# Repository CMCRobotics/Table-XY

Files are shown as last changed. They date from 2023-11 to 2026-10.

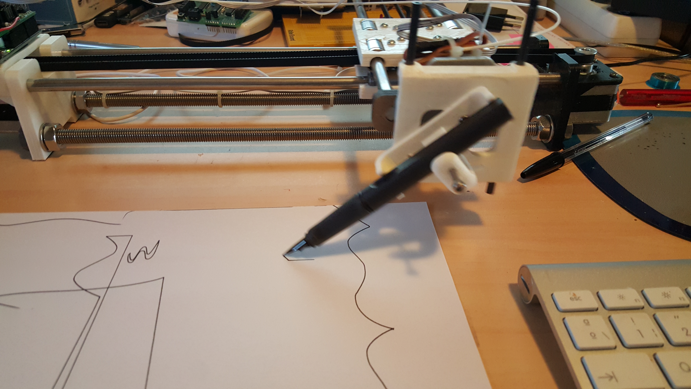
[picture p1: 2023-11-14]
mechanic/docs/Images General/2016-04-07_18.31.24.jpg

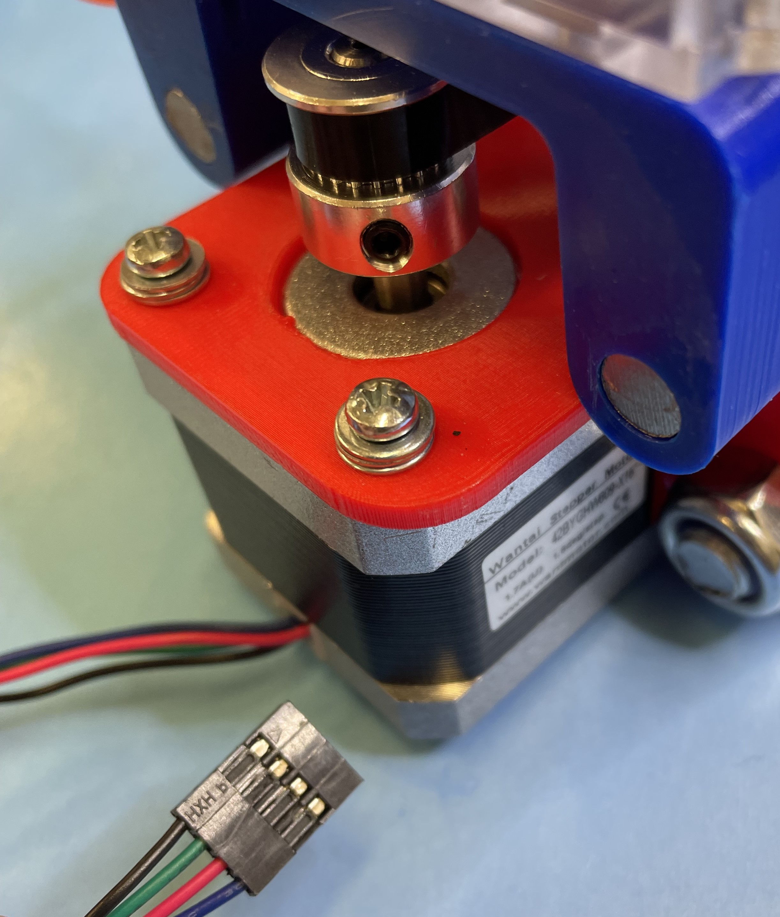
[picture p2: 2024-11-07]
assembly/Photos/IMG_9785.JPG

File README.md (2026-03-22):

# Table-XY
Development of a Table XY based on 4xiDraw

Directories:
- docs: 
- 	General documents

- components: 
- 	Components to be bought, related actions

- hardware: 
- 	documents related to Electronic hardware

- mechanic: 
-	Mechanic elements
-     mechanic / docs: documents related to mechanic elements
-     mechanic / Files: documents related to mechanical elements
-     mechanic / Printer3D-Prusa: documents related to Prusa Printer-3D

- photos: 
-	Photos of the assembly steps

- software: 
-	programs and related elements
-     software / docs: documents
-     software / Arduino: Arduino related programs

- wiki: 
-	elements for wiki page
-     wiki / images: Images
-     wiki / docs: Documents.

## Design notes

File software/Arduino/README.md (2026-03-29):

# Table-XY
Development of Arduino programs

Directories:
- UNO: 
-	programs related to Arduino UNO component
- 		UNO / grbl-servo-master: Original grbl-servo-master with M3/M5 action 
- 		UNO / TableXY_grbl: Modified grbl-servo-master transforming Zaxis movements into M3/M5 up/down pencil actions. IN DEVELOPEMENT
-							Versions.txt: details the modifications

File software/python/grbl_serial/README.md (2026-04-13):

# Serial GRBL

Python program for exchanging CGode files with a GRBL based device 

Based on simple_stream.py from https://github.com/gnea/grbl v1.1h

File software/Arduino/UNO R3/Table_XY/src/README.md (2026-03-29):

-------------------------------------------------------------------

Program modified by Jose Luis Gomez Costa, for converting Zaxis commands into Pencil up/down commands

	When Z command is detected in a Command line:
		- Mxx command is executed, depending on the value of Z movement:
			Z positive is Pencil up
			Z negative is Pencil down
			Only the sign is checked.
		- then the original command line is executed unmodified.
		
	This will imply always processing the Z axis, but as there is no hardware it will not interfere with the actual behaviour with a Pencil.

-------------------------------------------------------------------
# grbl-servo Original
grbl 0.9i with Servo motor support

GRBL 0.9i with servo motor support.
Use the PIN D11 to drive the servo. 
Use the commands M03 Sxxx (xxx between 0 and 255) to rotate the servo between 0-180.
The command M05 turn the servo to zero degrees.

you can change the pulse duration in the file spindle_control.c:

define RC_SERVO_SHORT     15       // Timer ticks for 0.6ms pulse duration  (9 for 0.6ms)

define RC_SERVO_LONG      32       // Timer ticks for 2.5 ms pulse duration  (39 for 2.5ms)     

define RC_SERVO_INVERT     1     // Uncomment to invert servo direction

If you want to have the servo working from 0 --> 180 degrees change RC_SERVO_SHORT and put 9, RC_SERVO_LONG and put 39
If you want invert the servo direction uncomment the line above.

I tested the code very well with 328p (Arduino Uno, Duemilanove etv), not with 2560 (Arduino Mega), but I think it would work well also with the Mega.

-------------------------------------------------------------------

The link for GRBL vanilla is: http://github.com/grbl/grbl

Grbl is a no-compromise, high performance, low cost alternative to parallel-port-based motion control for CNC milling. It will run on a vanilla Arduino (Duemillanove/Uno) as long as it sports an Atmega 328.

The controller is written in highly optimized C utilizing every clever feature of the AVR-chips to achieve precise timing and asynchronous operation. It is able to maintain up to 30kHz of stable, jitter free control pulses.

It accepts standards-compliant g-code and has been tested with the output of several CAM tools with no problems. Arcs, circles and helical motion are fully supported, as well as, all other primary g-code commands. Macro functions, variables, and most canned cycles are not supported, but we think GUIs can do a much better job at translating them into straight g-code anyhow.

Grbl includes full acceleration management with look ahead. That means the controller will look up to 18 motions into the future and plan its velocities ahead to deliver smooth acceleration and jerk-free cornering.

Licensing: Grbl is free software, released under the GPLv3 license.

For more information and help, check out our Wiki pages! If you find that the information is out-dated, please to help us keep it updated by editing it or notifying our community! Thanks!

Lead Developer [2011 - Current]: Sungeun(Sonny) K. Jeon, Ph.D. (USA) aka @chamnit

Lead Developer [2009 - 2011]: Simen Svale Skogsrud (Norway). aka The Originator/Creator/Pioneer/Father of Grbl.

The link for GRBL vanilla is: http://github.com/grbl/grbl

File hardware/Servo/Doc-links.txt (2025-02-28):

https://protosupplies.com/product/servo-motor-micro-sg92r/
https://forum.phpoc.com/articles/tutorials/347-servo-motor-how-to-control-servo-motor

https://docs.arduino.cc/learn/electronics/servo-motors/
Servo Hardware: https://en.wikipedia.org/wiki/Servo_(radio_control)

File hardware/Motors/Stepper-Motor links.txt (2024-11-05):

Half/Full step:
https://sea.omega.com/th/prodinfo/stepper_motors.html
https://www.automate.org/motion-control/case-studies/what-is-the-difference-between-full-stepping-the-half-stepping-and-the-micro-drive
Arduno: half/Full step: https://www.youtube.com/watch?v=cYAPK7xoISE

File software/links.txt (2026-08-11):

---------------------------------------------------------------------------
Description files: https://www.instructables.com/4xiDraw/General

---------------------------------------------------------------------------
Universal GCode sender: 
		https://universalgcodesender.com/
		https://github.com/winder/Universal-G-Code-Sender?tab=readme-ov-file
		
		UGS Platform (Rich): Run directly the exe in d:\Hobby\GRBL\ugsplatform-win\bin\
		UGS Clasic: Simple for sending direct commands to the Controller. Requires JAVA 61

---------------------------------------------------------------------------

Display/Simulate GCode work https://camotics.org/

---------------------------------------------------------------------------
GRBL: https://github.com/grbl/grbl/tree/master/grbl
      https://github.com/gnea/grbl
	  
GRBL updates: https://github.com/gnea
GRBL 1.1 https://github.com/gnea/grbl

GRBL 0.9 https://github.com/grbl/grbl/wiki/Configuring-Grbl-v0.9

GRBL 0.9i with Servo motor support: https://github.com/misan/grbl-servo

Pilot CNC via GCode with Arduino: https://letmeknow.fr/fr/blog/110-tuto-piloter-une-cnc-avec-arduino-et-grbl

Arduino Forum for GRBL: https://forum.arduino.cc/t/arduino-uno-r4-minima-grbl-upload-error/1385989

GRBL with servo: 	https://github.com/misan/grbl-servo	  

GRBL updates: https://github.com/gnea
GRBL 0.9 https://github.com/grbl/grbl/wiki/Configuring-Grbl-v0.9

Pilot CNC via GCode with Arduino: https://letmeknow.fr/fr/blog/110-tuto-piloter-une-cnc-avec-arduino-et-grbl

---------------------------------------------------------------------------
Documents on M et G Code:
	http://fr.insta3dp.com/info/3d-printer-g-code-commands-full-list-tutori-79272752.html

	https://gcodetutor.com/cnc-machine-training/cnc-g-codes.html

	https://linuxcnc.org/docs/2.8/html/gcode/gcode_fr.html

	https://www.cnccookbook.com/cnc-lathe-gcode-mcode-reference-list-turning/

	https://machiningconceptserie.com/m-code-cheat-sheet/

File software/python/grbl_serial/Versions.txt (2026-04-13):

Changelog

--------------------------------------------------------------------------------
Version: 0.1

Date:	09/04/2026
Author: Jose Luis Gomez Costa

	Initial Version

--------------------------------------------------------------------------------
Version: 0.101

Date:	09/04/2026
Author: Jose Luis Gomez Costa

	Modified the actions to display Version/program purpose
	
--------------------------------------------------------------------------------
Version: 0.102

Date:	11/04/2026
Author: Jose Luis Gomez Costa

	Adding Try-Except to input/output streams
	Added utils.py
	
--------------------------------------------------------------------------------
Version: 0.150

Date:	11/04/2026
Author: Jose Luis Gomez Costa

	with open, can not be used

--------------------------------------------------------------------------------
Version: 0.160

Date:	12/04/2026
Author: Jose Luis Gomez Costa

	log file stored in same directory as Gcode file or in present directory
	Trying ot create a log.log file throws an error if file does not exist yet
	
--------------------------------------------------------------------------------
Version: 0.200

Date:	12/04/2026
Author: Jose Luis Gomez Costa

	log.log file problem solved. 
		May be the directory was created/renamed after WSL being started.
		Therefore a problem with access rights.

--------------------------------------------------------------------------------
Version: 0.210

Date:	13/04/2026
Author: Jose Luis Gomez Costa

	Changed Directory name from serial_grbl to grbl_serial
	grbl_serial.py: 
		Added Description
		Printed (and to log if enabled) GRBL Version
		
--------------------------------------------------------------------------------
Version: 0.210

Date:	13/04/2026
Author: Jose Luis Gomez Costa

	Changed Directory name from serial_grbl to grbl_serial
	grbl_serial.py: 
		Added Description
		Printed (and to log if enabled) GRBL Version

--------------------------------------------------------------------------------
Version: 1.000

Date:	13/04/2026
Author: Jose Luis Gomez Costa

	First production Version

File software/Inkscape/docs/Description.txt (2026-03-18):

Salut,

Multi shape.svg: Inkscape fichier pour 2 figures
SVG.jpg: figures a dessiner, depuis Inkscape
Multi shape_0029.ngc: GCode pour 2 figures
Inkscape gcodetools: répertoire complet de l'extension GCodeTools avec le fichier phyton

Multi shape_0029.ngc:
	G00 Z1.000000: Z1.000000 monter l’outil à +1mm: zone livre

	G01 Z-1.000000 F100.0(Penetrate): Z-1.000000 descendre l’outil à -1mm, Fxxx: vitesse de rotation de l’outil

	G01 X129.643569 Y135.608775 Z-1.000000 F400.000000: déplacer l’outil dans l'axe XY, l’outil reste a -1mm

gcodetools.py:

	options.Zsafe: 
		-> Zsafe: auteur à partir de laquelle il est possible de bouger l’outil sans tracer (dans l’exemple: 1.00 mm). Ceci c'est une option qui est choisie dans Inkscape menu: Extensions/GCodeTools/Chemin vers GCode/Preferences
	options.Zdepth 
		-> Zdepth: profondeur à laquelle descendre l’outil pour tracer (dans l’exemple: -1.00 mm). Ceci c'est une option qui est choisie dans Inkscape, et transféré dans le fichier Multi shape.svg.

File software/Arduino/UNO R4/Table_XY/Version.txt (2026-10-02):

Detail of versions
	Conversion of TableXY GRBL 0.9i with Servo as spindle for arduino Uno R4 WiFi

ATTENTION:
	SOME parts of original GRBL code are commented out until their conversion to Arduino Uno R4 is made

----------------------------------------
Version: R4 0.003

Date:	27/06/2026
Author: Jose Luis Gomez Costa

	Starting coding

----------------------------------------
Version: R4 0.004

Date:	27/06/2026
Author: Jose Luis Gomez Costa

	Added Data Flash functions

----------------------------------------
Version: R4 0.005

Date:	28/06/2026
Author: Jose Luis Gomez Costa

	Adding Stepper functions

----------------------------------------
Version: R4 0.006

Date:	29/06/2026
Author: Jose Luis Gomez Costa

	Adding Stepper System

----------------------------------------
Version: R4 0.007

Date:	30/06/2026
Author: Jose Luis Gomez Costa

	Adding Control inputs

----------------------------------------
Version: R4 0.008

Date:	01/07/2026
Author: Jose Luis Gomez Costa

	Adding Control input functions

----------------------------------------
Version: R4 0.009

Date:	01/07/2026
Author: Jose Luis Gomez Costa

	Added Limit (almost), Cooling, most of functions

----------------------------------------
Version: R4 0.010

Date:	01/07/2026
Author: Jose Luis Gomez Costa

	Adding
		- Limit
		- Servo spindle

----------------------------------------
Version: R4 GRBL 0.011

Date:	03/07/2026
Author: Jose Luis Gomez Costa

	Added
		- delay_us and delay_ms
		- Servo spindle

	Adding
		- Limit

----------------------------------------
Version: R4 GRBL 0.020

Date:	04/07/2026
Author: Jose Luis Gomez Costa

	Added
		- Limit

	To be checked:
		- TODO sentences:
			- limit.cpp: verify active/not active sens of limit bits
			- system.cpp: verify active/not active sens of limit bits
			- planner.cpp: verify units of Counters for Period/delay/Pulse high
		- Add disclaimer

----------------------------------------
Version: R4 GRBL 0.030

Date:	05/07/2026
Author: Jose Luis Gomez Costa

	To be checked:
		- TODO sentences:
			- system.cpp:
				Line 331:  TODO: correct for 8 bit/16bit registers
			- planner.cpp: verify units of Counters for Period/delay/Pulse high

		- Add disclaimer

----------------------------------------
Version: R4 GRBL 0.040

Date:	06/07/2026
Author: Jose Luis Gomez Costa

	To be checked:
		- TODO sentences:
			- system.cpp:
				Line 331:  TODO: correct for 8 bit/16bit registers
		- planner.cpp: verify units of Counters for delay/Pulse high
		- Pulse Delay / Pulse High: verify setting place

		- Add disclaimer

----------------------------------------
Version: R4 GRBL 0.050

Date:	06/07/2026
Author: Jose Luis Gomez Costa

	- TODO sentences:
		- system.cpp:
			Line 331:  TODO: correct for 8 bit/16bit registers

	- Add disclaimer

----------------------------------------
Version: R4 GRBL 0.100

Date:	07/07/2026
Author: Jose Luis Gomez Costa

	- TODO sentences:
		- system.cpp:
			Line 331:  TODO: correct for 8 bit/16bit registers

	- Added disclaimer and Copyrights

----------------------------------------
Version: R4 GRBL 0.200

Date:	07/07/2026
Author: Jose Luis Gomez Costa

	- TODO sentences:
		- system.cpp:
			Line 331:  TODO: correct for 8 bit/16bit registers

	- main.cpp MUST have setup()/loop() functions

----------------------------------------
Version: R4 GRBL 0.205

Date:	07/07/2026
Author: Jose Luis Gomez Costa

	- TODO sentences:
		- system.cpp:
			Line 331:  TODO: correct for 8 bit/16bit registers

	Testing Serial print

----------------------------------------
Version: R4 GRBL 0.207

Date:	08/07/2026
Author: Jose Luis Gomez Costa

	- TODO sentences:
		- system.cpp:
			Line 331:  TODO: correct for 8 bit/16bit registers

	Testing Serial print:
		Added TEST-1/2 TestPoints
		probe and coolant commented out

----------------------------------------
Version: R4 GRBL 0.300

Date:	09/07/2026
Author: Jose Luis Gomez Costa

	- TODO sentences:
		- system.cpp:
			Line 331:  TODO: correct for 8 bit/16bit registers

	Testing Serial print:
		Added TEST-1/2 TestPoints
		probe and coolant commented out

		- To be thorougly checked the TX serial functions. It seems the TX Circular buffer is not correctly updated for discarding old inputs
		- TX/RX exchange seems to work OK, except previous point

----------------------------------------
Version: R4 GRBL 0.400

Date:	10/07/2026
Author: Jose Luis Gomez Costa

	- TODO sentences:
		- system.cpp:
			Line 331:  TODO: correct for 8 bit/16bit registers

	Testing Serial print:
		Complete refurbishement of Serial TX functions

----------------------------------------
Version: R4 GRBL 0.500

Date:	10/07/2026
Author: Jose Luis Gomez Costa

	- TODO sentences:
		- system.cpp:
			Line 331:  TODO: correct for 8 bit/16bit registers
		- Correct print.cpp functions for acepting the new serial_write(char *string)
		- Store in Flash the corrected parameters

----------------------------------------
Version: R4 GRBL 0.600

Date:	10/07/2026
Author: Jose Luis Gomez Costa

	- Corrected print.cpp / utils.cpp
		Functions for accepting the new serial_write(char *string)

	- TODO sentences:
		- system.cpp:
			Line 331:  TODO: correct for 8 bit/16bit registers
		- Transform all functions:
			from printPgmString(char *s) to printString(char *s)

		- Store in Flash the corrected parameters

----------------------------------------
Version: R4 GRBL 0.610

Date:	10/07/2026
Author: Jose Luis Gomez Costa

	- Transform all functions:
			from printPgmString(char *s) to printString(char *s)

	- TODO:
		- system.cpp:
			Line 331:  TODO: correct for 8 bit/16bit registers
		- Test storing parameters in Flash

----------------------------------------
Version: R4 GRBL 0.616

Date:	10/07/2026
Author: Jose Luis Gomez Costa

	- Tested storing parameters in Flash

	- TODO:
		- system.cpp:
			Line 331:  TODO: correct for 8 bit/16bit registers
		- Enable Probe and coolant

Test process:
	- OK: Verify / Update Parameters from R3 to R4

	- Create files with XY:
		1- Large positive slope
		- Speed 100
		- Speed 50

		2- Large negative slope
		- Speed 100
		- Speed 50

	  R3: note Step Pulse frequency
	  R4: check compliance

	- Check Limit pins
	- Check Control pins
	- Test Servo

	Testing:
		- XY Large positive:
			ERROR: Step pulse is cleared at next ISR rather than after pulseWidth setting (10usec as per $0 parameter)
			Changing $0 does not affect the placement of the IRQ

----------------------------------------
Version: R4 GRBL 0.620

Date:	10/07/2026
Author: Jose Luis Gomez Costa

	- TODO:
		- system.cpp:
			Line 331:  TODO: correct for 8 bit/16bit registers
		- Enable Probe and coolant

Test process:
	- OK: Verify / Update Parameters from R3 to R4

	- Create files with XY:
		1- Large positive slope
		- Speed 100
		- Speed 50

		2- Large negative slope
		- Speed 100
		- Speed 50

	  R3: note Step Pulse frequency
	  R4: check compliance

	- Check Limit pins
	- Check Control pins
	- Test Servo

	Testing:
		- XY Large positive:
			ERROR: Step pulse is cleared at next ISR rather than after pulseWidth setting (10usec as per $0 parameter)
			Changing $0 does not affect the placement of the IRQ
			Bug Corrected: wrongly calculated parameter MOTOR_TICK_PER_USEC and MOTOR_TICK_PER_SEC

----------------------------------------
Version: R4 GRBL 0.625

Date:	10/07/2026
Author: Jose Luis Gomez Costa

	- TODO:
		- system.cpp:
			Line 331:  TODO: correct for 8 bit/16bit registers
		- Enable Probe and coolant

Test process:
	- OK: Verify / Update Parameters from R3 to R4

	- Check R4 compliance with respecto to R3 values
			#Pulse Y per Pulse X
			Period X [usec]
			Period Y  [usec]
			Interruption Period  [usec]
			#Interruptions per Pulse Y
			Length Interruption [usec]

		For files with XY:
			1- Large positive slope
			- Speed 100
			- Speed 50

			2- Large negative slope
			- Speed 100
			- Speed 50

	- OK: Check Step Pulse width
	- Check Limit pins
	- Check Control pins
	- Test Servo

	Testing:
		- XY Large positive
			To be checked: memory width for ISR main function period Counters
						st.exec_segment->cycles_per_tick (MUST be uint32_t). defined in typedef struct { ... } segment_t;

----------------------------------------
Version: R4 GRBL 0.650

Date:	11/07/2026
Author: Jose Luis Gomez Costa

	- TODO:
		- system.cpp:
			Line 331:  TODO: correct for 8 bit/16bit registers

		- Enable Probe and Coolant
			functions commented out when referenced:
				void probe_state_monitor()
				uint8_t probe_get_state()
				void probe_init()

				void coolant_init()
				void coolant_stop()
				void coolant_set_state(uint8_t mode)
				void coolant_run(uint8_t mode)

Test process:
	- OK: Verify / Update Parameters from R3 to R4

	- Check R4 compliance with respecto to R3 values
			#Pulse Y per Pulse X
			Period X [usec]
			Period Y  [usec]
			Interruption Period  [usec]
			#Interruptions per Pulse Y
			Length Interruption [usec]

		For files with XY:
			1- Large positive slope
			- Speed 100
			- Speed 50

			2- Large negative slope
			- Speed 100
			- Speed 50

	- OK: Check Step Pulse width
	- Check Limit pins
	- Check Control pins
	- Test Servo

	Testing:
		- XY Large positive
		- Commented out any reference to Probe / Coolant
		- Updating AMASS cutoff level for CPU: 48MHz
		- step_pulse_stop = false; at Pulse stop function
		- Commented out Stopping of timer when changing the Period
		- Added Test signals
		- Disabled Limit & Control AGT1 Interruption

----------------------------------------
Version: R4 GRBL 0.680

Date:	11/07/2026
Author: Jose Luis Gomez Costa

	- TODO:
		- system.cpp:
			Line 331:  TODO: correct for 8 bit/16bit registers

		- Enable Probe and Coolant
			functions commented out when referenced:
				void probe_state_monitor()
				uint8_t probe_get_state()
				void probe_init()

				void coolant_init()
				void coolant_stop()
				void coolant_set_state(uint8_t mode)
				void coolant_run(uint8_t mode)

Test process:
	- OK: Verify / Update Parameters from R3 to R4

	- Check R4 compliance with respecto to R3 values
			#Pulse Y per Pulse X
			Period X [usec]
			Period Y  [usec]
			Interruption Period  [usec]
			#Interruptions per Pulse Y
			Length Interruption [usec]

		For files with XY:
			1- Large positive slope
			- Speed 100
			- Speed 50

			2- Large negative slope
			- Speed 100
			- Speed 50

	- OK: Check Step Pulse width
	- Check Limit pins
	- Check Control pins
	- Test Servo

	Testing:
		- XY Large positive
		- Commented out any reference to Probe / Coolant
		- Updating AMASS cutoff level for CPU: 48MHz
		- step_pulse_stop = false; at Pulse stop function
		- Commented out Stopping of timer when changing the Period
		- Added Test signals
		- Disabled Limit & Control AGT1 Interruption
		- All memories / calculations for direction/Step pins are 16bits
		- step_invert_mask dir_invert_mask : 16 bits
		- direction_bits : 16 bits
		- Serial TX buffer: 1000
		- Enabled Stopping of timer when changing the Period
		- TEST_2: TX Interruption

----------------------------------------
Version: R4 GRBL 0.700

Date:	12/07/2026
Author: Jose Luis Gomez Costa

	Added posibility of using Hardware debugger, in that case:
		Mode:
			If Normal mode is used:
			SCI 9: Program communication
			SCI 2: Not used

			If Debug mode is used:
			SCI 9: Debug exchange with IDE
			SCI 2: Program communication
		Selection is made in lib/common/include/debug.have

----------------------------------------
Version: R4 GRBL 0.750

Date:	14/07/2026
Author: Jose Luis Gomez Costa

	#define COREXY: uncomented

----------------------------------------
Version: R4 GRBL 0.800

Date:	14/07/2026
Author: Jose Luis Gomez Costa

	Parameter definitions:
		- For generating normal reports to UGS: $10 = 3    (status report mask:00000011)

	To be checked:
		UGS: Manual mouvements
			Set +X -> Moves +X
			Set +Y -> Moves +X?

			Set -Y -> Moves -Y
			Set -X -> Moves -Y?

			Set +Z -> Moves +Z
			Set -Z -> Moves +Z?

----------------------------------------
Version: R4 GRBL 0.807

Date:	15/07/2026
Author: Jose Luis Gomez Costa

	DEBUG + Serial SCI2
		- void serial_init(): PSEL code for SCI9 and SCI2 are different

	To be checked:
		Reset to 0: G10P0L20X0Y0Z0 does not seem to work
		MPos / WPos can not be cleared
		[G54:10.000,20.000,10.000] whils in R3 are ALL 0
			Set as: G10P0L20X0Y0Z0

		UGS: Manual mouvements
			Set +X -> Moves +X
			Set +Y -> Moves +X?

			Set -Y -> Moves -Y
			Set -X -> Moves -Y?

			Set +Z -> Moves +Z
			Set -Z -> Moves +Z?

	- config.h:
		Uncomment: #define REPORT_ECHO_LINE_RECEIVED // Default disabled. Uncomment to enable.
		Nothing to extract.

----------------------------------------
Version: R4 GRBL 0.810

Date:	16/07/2026
Author: Jose Luis Gomez Costa

	planner.cpp/h
		typedef struct { } plan_block_t : block->direction_bits must be unit16 bits, not 8 bits
		This created the wrong settings for Motor Direction and Reports.

	To be checked:
		Uncomment Probe
		Uncomment Limits
		Uncomment Controls
		Uncomment Coolant
		Test Pencil-Spindle

		Some times:
			- The Step-clear interruption is not executed, the Step pulse is cleared in the next interruption.
			- UGCodeSender JogController seems to block CPU

----------------------------------------
Version: R4 GRBL 0.820

Date:	16/07/2026
Author: Jose Luis Gomez Costa

	To be checked:
		Probe
		Limits
		Controls
		Coolant
		Pencil-Spindle

		Some times:
			- The Step-clear interruption is not executed, the Step pulse is cleared in the next interruption.
			- UGCodeSender JogController seems to block CPU

	Testing:
		Disabled //Test start ... // Test End
			Probe
			Coolant
			Pencil-Spindle

		Limits:
			LimitX/Y: not working

----------------------------------------
Version: R4 GRBL 0.820

Date:	16/07/2026
Author: Jose Luis Gomez Costa

	To be checked:
		Probe
		Limits
		Controls
		Coolant
		Pencil-Spindle

		Some times:
			- The Step-clear interruption is not executed, the Step pulse is cleared in the next interruption.
			- UGCodeSender JogController seems to block CPU

	Testing:
		Disabled //Test start ... // Test End
			Probe
			Coolant
			Pencil-Spindle

		Limits:
			LimitX/Y: not working
			Pull-up not correctly defined on all pins

----------------------------------------
Version: R4 GRBL 0.830

Date:	18/07/2026
Author: Jose Luis Gomez Costa

	To be checked:
		Probe
		Limits
		Controls
		Coolant
		Pencil-Spindle

		Some times:
			- The Step-clear interruption is not executed, the Step pulse is cleared in the next interruption.
			- UGCodeSender JogController seems to block CPU

	Testing:
		Disabled //Test start ... // Test End
			Probe
			Coolant
			Pencil-Spindle

		Limits:
			LimitX/Y: working? but no indication is sent to the UGCodeSender
			R3: RED ALARM banner, message: An unexpected error was detected: ALARM: Hard limit
			R4: no more pulses, but keep stuck
				but, when resetting, following broken message appears: An unexpected error was detected: ALARM: [
			Added __NOP() in void protocol_execute_realtime(): Interruptions not executed?
			Eliminated: uint8_t get_limit_pin_mask(uint8_t axis_idx)

----------------------------------------
Version: R4 GRBL 0.833

Date:	19/07/2026
Author: Jose Luis Gomez Costa

	To be checked:
		Probe
		Limits
		Controls
		Coolant
		Pencil-Spindle

		Some times:
			- The Step-clear interruption is not executed, the Step pulse is cleared in the next interruption.
			- UGCodeSender JogController seems to block CPU

	Limit tests:
		void protocol_execute_realtime(), uncommented part of       } while (bit_isfalse(sys.rt_exec_state,EXEC_RESET));
	 	Action is almost corrrect: detected Alarm as in R3, only message is not quite correct:
	 		An unexpected error was detected: ALARM: [<Alarm,MPos:15.980,0.000,0.000,WPos:15.980,0.000,0.000>
		Although it is COMMENTED OUT in R3??

		#define LIMIT_CONTROL_ISR_PERIOD_US (5000) instead of (1000)

----------------------------------------
Version: R4 GRBL 0.850

Date:	19/07/2026
Author: Jose Luis Gomez Costa

	To be checked:
		Probe
		Limits
		Controls
		Coolant
		Pencil-Spindle

		Some times:
			- The Step-clear interruption is not executed, the Step pulse is cleared in the next interruption.
			- UGCodeSender JogController seems to block CPU

	Limit tests:
		All modules retourned to its R3 general steps.
		The problem seemd to come form the fact that the Serial transfer of report_alarm_message() was divided in 3 distinct transfers?
		Now all message is sent in one go.

----------------------------------------
Version: R4 GRBL 0.860

Date:	19/07/2026
Author: Jose Luis Gomez Costa

	To be checked:
		Limits
			X (D9) OK
			Y (D10) OK
			Z (D12) OK
		Controls
			Abort (A0) OK
			Feed Hold(A1) OK
			Resume (A2) OK
			E-Stop (Analog Pin3) OK

		Probe
		Coolant
		Pencil-Spindle

		Some times:
			- The Step-clear interruption is not executed, the Step pulse is cleared in the next interruption.
			- UGCodeSender JogController seems to block CPU

----------------------------------------
Version: R4 GRBL 0.870

Date:	19/07/2026
Author: Jose Luis Gomez Costa

	To be checked:
		Pencil-Spindle
			Z: +1	OK
			Z: -1	OK
		Probe
			Only enable and then check that all works OK
		Coolant
			Only enable and then check that all works OK

		Some times:
			- The Step-clear interruption is not executed, the Step pulse is cleared in the next interruption.
			- UGCodeSender JogController seems to block CPU

----------------------------------------
Version: R4 GRBL 0.875

Date:	19/07/2026
Author: Jose Luis Gomez Costa

	To be checked:
		Probe OK
			Enabled, then check that all works OK

		Coolant
			Only enable and then check that all works OK

		Some times:
			- The Step-clear interruption is not executed, the Step pulse is cleared in the next interruption.
			- UGCodeSender JogController seems to block CPU

----------------------------------------
Version: R4 GRBL 0.880

Date:	19/07/2026
Author: Jose Luis Gomez Costa

	To be checked:
		Coolant OK
			Enabled. Check that all works OK

		Delay Direction-Step

	Some times:
		- The Step-clear interruption is not executed, the Step pulse is cleared in the next interruption.
		- UGCodeSender JogController seems to block CPU

----------------------------------------
Version: R4 GRBL 0.890

Date:	19/07/2026
Author: Jose Luis Gomez Costa

	To be checked:
		Delay Direction-Step

	Some times:
		- The Step-clear interruption is not executed, the Step pulse is cleared in the next interruption.
		- UGCodeSender JogController seems to block CPU

----------------------------------------
Version: R4 GRBL 0.897

Date:	20/07/2026
Author: Jose Luis Gomez Costa

	Being checked:
		Delay Direction-Step
		Wrongly defined: uint8_t step_bits -> uint16_t step_bits
		Completely wrong timing for all Motor ISR interruptions, to be checked the Register definitions

		Added TEST_1/2 blocked Cooling/Probe

	To be checked:
		- The Step-clear interruption is not executed, the Step pulse is cleared in the next interruption.
		- UGCodeSender JogController seems to block CPU

----------------------------------------
Version: R4 GRBL 0.902

Date:	23/07/2026
Author: Jose Luis Gomez Costa

	Being checked:
		Delay Direction-Step
		Wrongly defined: uint8_t step_bits -> uint16_t step_bits
		When sending data, wrongly reading PODR rather than PIDR
		wrong timing: Problem comes form the fact that the TestPoint is not correctly stored between creation and CMPA access

		Added TEST_1/2 blocked Cooling/Probe

	To be checked:
		- The Step-clear interruption is not executed, the Step pulse is cleared in the next interruption.
		- UGCodeSender JogController seems to block CPU

----------------------------------------
Version: R4 GRBL 0.903

Date:	23/07/2026
Author: Jose Luis Gomez Costa

	To be checked:
		- Motor ISR sometimes are longuer than normally:
			- Is due to AGT1 interruption?
		- The Step-clear interruption is not executed, the Step pulse is cleared in the next interruption.
		- UGCodeSender JogController seems to block CPU

----------------------------------------
Version: R4 GRBL 0.910

Date:	23/07/2026
Author: Jose Luis Gomez Costa

	Being checked:
		- Motor ISR sometimes are longuer than normally:
			- Is due to AGT1 interruption?
			Main ISR: TET_3
			Delay/Pulse end: TEST_1
			AGT1: TEST_2

	To be checked:
		- The Step-clear interruption is not executed, the Step pulse is cleared in the next interruption.
		- UGCodeSender JogController seems to block CPU

----------------------------------------
Version: R4 GRBL 0.913

Date:	23/07/2026
Author: Jose Luis Gomez Costa

	Being checked:
		- Motor ISR sometimes are longuer than normally:
			- Is due to AGT1 interruption?
			Main ISR: TET_3
			Delay/Pulse end: TEST_1
			AGT1: TEST_2
			Re-enable interruptions inside ISR AGT1
			Changed Interruption Priorities: OK

	To be checked:
		- The Step-clear interruption is not executed, the Step pulse is cleared in the next interruption.
		- UGCodeSender JogController seems to block CPU

----------------------------------------
Version: R4 GRBL 0.916

Date:	23/07/2026
Author: Jose Luis Gomez Costa

	Being checked:
		- The Step-clear interruption is not executed, the Step pulse is cleared in the next interruption.
		Giving higher priorities to Step Pulse seems to have solved the problem

	To be checked:
		- UGCodeSender JogController seems to block CPU

----------------------------------------
Version: R4 GRBL 0.920

Date:	24/07/2026
Author: Jose Luis Gomez Costa

	To be checked:
		- UGCodeSender JogController seems to block CPU

----------------------------------------
Version: R4 GRBL 0.925

Date:	25/07/2026
Author: Jose Luis Gomez Costa

	Testing Step Pulse width for checking too wide-short pulses:OK

	To be checked:
		- UGCodeSender JogController seems to block CPU

----------------------------------------
Version: R4 GRBL 0.930

Date:	26/07/2026
Author: Jose Luis Gomez Costa

	Comparing Speed period with R3. No Delay

	To be checked:
		- UGCodeSender JogController seems to block CPU

----------------------------------------
Version: R4 GRBL 0.935

Date:	26/07/2026
Author: Jose Luis Gomez Costa

	Comparing Speed period with R3. No Delay:
		- 5 Times too slow compared to R3
		- Test:
			stepper.cpp Keep AMAS level as for R3

	To be checked:
		- UGCodeSender JogController seems to block CPU

----------------------------------------
Version: R4 GRBL 0.936

Date:	27/07/2026
Author: Jose Luis Gomez Costa

	Comparing Speed period with R3. No Delay:
		- 5 Times too slow compared to R3
		- Test:
			stepper.cpp Keep AMAS level as for R3. Not OK

	Testing: OK
		- UGCodeSender JogController seems to block CPU

----------------------------------------
Version: R4 GRBL 0.938

Date:	27/07/2026
Author: Jose Luis Gomez Costa

	Comparing Speed period with R3. No Delay:
		- 5 Times too slow compared to R3
		- Test:
			- stepper.cpp No OK
				Keep AMAS level as for R3
			- stepper.cpp
				Update AMASS_LEVELx (F_CPU * 3)/(x)) 48MHz = 16MHz * 3
				void st_prep_buffer():
					Manual correction of the MainISR Period: %/5
					      prep_segment->cycles_per_tick = cycles * 0.2; // Period / 5

	Testing: OK
		- UGCodeSender JogController seems to block CPU:  OK

----------------------------------------
Version: R4 GRBL 0.940

Date:	27/07/2026
Author: Jose Luis Gomez Costa

	Comparing Speed period with R3. No Delay:
		- 5 Times too slow compared to R3
		- Test:
			- stepper.cpp
				Update AMASS_LEVELx (F_CPU * 3)/(x)) 48MHz = 16MHz * 3
				void st_prep_buffer():
					Manual correction of the MainISR Period: % by 5
					      prep_segment->cycles_per_tick = cycles * 0.2; // Period / 5

----------------------------------------
Version: R4 GRBL 0.950

Date:	27/07/2026
Author: Jose Luis Gomez Costa

	- SCI Debug parameters to debug_cpu_r7fa4m1ab.h in GRBL include
		- Disable CPU Debug: OK (SCI-9)
	- Comment out use of Test1/2 pins: OK (Probe/Coolant enabled)

	- Compare Speed period with R3. No Delay:
		- X / Y (Fxx)
			- 10000 / 15000
				- F50
				- F100
			-10000 / 20000
				- F50
				- F100

----------------------------------------
Version: R4 GRBL 0.952

Date:	27/07/2026
Author: Jose Luis Gomez Costa

	All test OK.
	Check with Table XY

----------------------------------------
Version: R4 GRBL 0.960

Date:	07/08/2026
Author: Jose Luis Gomez Costa

	Corrected Servo Pencil PWM values
		spindle_control.h
		cpu_map_r7fa4m1ab.h

	Not Correct, fcn_servo_time_high(angle) must be differently calculated when Inverted and when not

----------------------------------------
Version: R4 GRBL 0.962

Date:	10/08/2026
Author: Jose Luis Gomez Costa

	Corrected Servo Pencil PWM values
		spindle_control.h
		cpu_map_r7fa4m1ab.h

	Not Correct, fcn_servo_time_high(angle) must be differently calculated when Inverted and when not
	Not finished

----------------------------------------
Version: R4 GRBL 0.963

Date:	10/08/2026
Author: Jose Luis Gomez Costa

	Corrected Servo Pencil PWM values
		spindle_control.h
		cpu_map_r7fa4m1ab.h

	Testing

----------------------------------------
Version: R4 GRBL 0.965

Date:	10/08/2026
Author: Jose Luis Gomez Costa

	Checking $P Menu outcome
		- lib/../debug_cpu_r7fa4m1ab.h
			Debugging option: #define SCI_MODE_DEBUG YES

----------------------------------------
Version: R4 GRBL 0.967

Date:	10/08/2026
Author: Jose Luis Gomez Costa

	$P Menu outcome
		- It works when using SCI auxiliar
		- Re-check with standard USB:
			Error is generated
			$A is also blocking?
		- check with Debug

----------------------------------------
Version: R4 GRBL 0.968

Date:	10/08/2026
Author: Jose Luis Gomez Costa

	$P/$I Menu outcome
		Respective Build Info are defines, do not store in EEPORM

	Testing $A: in process
		Registers MUST be set as 1/2/4 bytes
		Do NOT print more than one Register

----------------------------------------
Version: R4 GRBL 0.970

Date:	11/08/2026
Author: Jose Luis Gomez Costa

	Testing $A: deprecated
		As Registers can be 8/16/32 bits, too complicated to select, prone to memory access errors
		Instead, $A will return the data of an array of 10 * 32 bits.
			- Array name: debug_data
		 	- it can be filled with the desired data at specific positions under program Control
			- User program must control the filling process, access storage, etc.

----------------------------------------
Version: R4 GRBL 0.971

Date:	11/08/2026
Author: Jose Luis Gomez Costa

	Commented out: Debugging option: #define SCI_MODE_DEBUG YES

----------------------------------------
Version: R4 GRBL 0.972

Date:	11/08/2026
Author: Jose Luis Gomez Costa

	The Menu answer to $P, MUST be enclosed between [], Othewrise errors are generated at receiving program UGS

----------------------------------------
Version: R4 GRBL 0.973

Date:	11/08/2026
Author: Jose Luis Gomez Costa

	debug_data array length is defined in system.h:
		#define DEBUG_DATA_ARRAY_LENGTH

----------------------------------------
Version: R4 GRBL 0.974

Date:	12/08/2026
Author: Jose Luis Gomez Costa

	Only the files actually modified by me are marqued with my Copyright

----------------------------------------
Version: R4 GRBL 0.975

Date:	20/08/2026
Author: Jose Luis Gomez Costa

	Minimum text in comments

----------------------------------------
Version: R4 GRBL 0.976

Date:	20/08/2026
Author: Jose Luis Gomez Costa

	To be checked: M5 generates a 330ns pulse -> this might destroy the servo?
	Wrong setting for Maximum / Minimum Angle.
	It depends on Servo:
		- SM_S2309S: +/- 60deg (900 to 2100 useg)
		- SG90: +/- 90 deg (2 to 1 msec)

	Therefore Pencil (Spindle) is completely refurbished:
		M3/M4: Pencil Down. M3Sxx Sxx is discarded, PWM value is fixed
		M5: Pencil Up.PWM value is fixed

----------------------------------------
Version: R4 GRBL 0.977

Date:	21/08/2026
Author: Jose Luis Gomez Costa

	Testing Servo
	Modification in #defines names

----------------------------------------
Version: R4 GRBL 0.978

Date:	27/08/2026
Author: Jose Luis Gomez Costa

	Testing Servo:
		Servo movement: 90deg

----------------------------------------
Version: R4 GRBL 0.979

Date:	31/08/2026
Author: Jose Luis Gomez Costa

	Testing Servo:
		Servo movement: 90deg
		Not Inverted

----------------------------------------
Version: R4 GRBL 0.980

Date:	01/10/2026
Author: Jose Luis Gomez Costa

	spindle_control.cpp
		Transfered to spindle_control.h #define RC_SERVO_INVERT

	Spindle parameters:
		Adapted to specific Servo
		Added Servo for SG92R:
			Servo movement: 90deg
			Inverted

----------------------------------------
Version: R4 GRBL 0.981

Date:	02/10/2026
Author: Jose Luis Gomez Costa

	spindle_control.h/cpp:
		#define RC_SERVO_INVERT: transformed to boolean true/false
	
	spindle_control.h:
		Spindle parameters Servo SG92R:
			Servo Freq: 60hz
			M5 pulse: 640 usec
			M03 S85 pulse:	2431 usec	GCODE_PENCIL_DOWN
			M03 S00 pulse:	640	 usec	GCODE_PENCIL_UP

			Not Inverted

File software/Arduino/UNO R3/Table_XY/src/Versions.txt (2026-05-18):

Detail of versions

----------------------------------------
Version: 0.1

Date:	21/03/2026
Author: Jose Luis Gomez Costa

	Initial Version
	
----------------------------------------
Version: 0.11

Date:	21/03/2026
Author: Jose Luis Gomez Costa

	gcode.c/h
		Eliminated all Z related commands, if present -> STATUS_GCODE_UNSUPPORTED_COMMAND
	
	report.c
		Added Pencil up/down Version indications

----------------------------------------
Version: 0.2

Date:	22/03/2026
Author: Jose Luis Gomez Costa

	gcode.c/h
		Eliminated all Z related commands, if present -> STATUS_GCODE_UNSUPPORTED_COMMAND
		Strange tweak to be done:
			// commented out, otherwise FAIL status appears when executing: G00 Zxxxx command
			// if (value_words) { FAIL(STATUS_GCODE_UNUSED_WORDS); } // [Unused words]

	report.c
		Added Pencil up/down Version indications
		Added Menu: $P: displays Pencil Build information

----------------------------------------
Version: 0.3

Date:	22/03/2026
Author: Jose Luis Gomez Costa

	The previous approach is too complex, too many errors when modifying the actual processing 
	
	A  simpler one is chosen:
		When Z command is detected:
			- Mxx command is executed
			- then the original command line is executed unmodified.
		Process: 
			1.0 Keep OriginalLine unmodified
			2.0 Command Line is parsed:	
				2.1 if no Z command is found, jump to 3.0
				2.2 if Z command is found: Generate a Dummy CommandLine with the M03 or M05
				2.3 Execute Dummy CommandLine
				2.3.1 If error detected, jump in 4.0
			3.0 Execute OriginalLine
			4.0 Return with:
				detected error
				or OK if none
		
	This will imply always processing the Z axis, but as there is no hardware it will not interfere with the actual behaviour with a Pencil.

	OriginalLine: one line of 0-terminated G-Code.
		The line is assumed to contain only uppercase characters and signed floating point values (no white-space).
		Comments and block delete characters have been removed.
		
	Zvalue
		value = floating Point
		value >= 2.0 -> Pencil Up
		value  < 2.0 -> Pencil Down

	pencil.h:
		All definitions for the Pencil behaviour
		
----------------------------------------
Version: 0.35

Date:	23/03/2026
Author: Jose Luis Gomez Costa

	pencil.h:
		Modified, Version data transferred to version_pencil.h

	pencil.c:
		All actions for adjusting pencil processing

	grbl.h:
		added new .h files

	TODO!!!!!!: change old name of gcode.c 		uint8_t gc_execute_line(char *line) 
	
----------------------------------------
Version: 0.36

Date:	23/03/2026
Author: Jose Luis Gomez Costa

	gcode.c/.h:
			Renamed uint8_t gc_execute_line(char *line) to uint8_t gc_execute_line_actual(char *line)

----------------------------------------
Version: 0.37

Date:	23/03/2026
Author: Jose Luis Gomez Costa

	Added Test functions for transferring data via Serial Port
	See grbl.h
	
----------------------------------------
Version: 0.371

Date:	23/03/2026
Author: Jose Luis Gomez Costa

	pencil_version.h: Wrong date GRBL_BUILD_PENCIL_DAY

----------------------------------------
Version: 0.38

Date:	23/03/2026
Author: Jose Luis Gomez Costa

	pencil.h: Modified Z_AXIS_LIMIT to 0.5

----------------------------------------
Version: 0.385

Date:	23/03/2026
Author: Jose Luis Gomez Costa

	pencil.h:
		Modified ACTION_PENCIL_UP "M3"
		Modified ACTION_PENCIL_DOWN "M5"
		Modified Z_AXIS_LIMIT  1.0000
		
----------------------------------------
Version: 0.400

Date:	24/03/2026
Author: Jose Luis Gomez Costa

	pencil.c:
		Simplifyed the detection of Z movement:
			Z positive is Pencil up
			Z negative is Pencil down
			Only the sign is checked.

	pencil.h:
		Modified names ACTION_PENCIL_xx ->  GCODE_PENCIL_xx

----------------------------------------
Version: 0.401

Date:	24/03/2026
Author: Jose Luis Gomez Costa

	pencil.c:
		Corrected compilation errors
		
----------------------------------------
Version: 0.505

Date:	27/03/2026
Author: Jose Luis Gomez Costa

	pencil.h:
		GCODE_PENCIL_UP: Added servo movement:

		Inverted Gcode Servo actions
		
----------------------------------------
Version: 0.600

Date:	27/03/2026
Author: Jose Luis Gomez Costa

	pencil.h:
		M03 S motion to 86deg.
	
	system.c / report.c:
		Added display of Menu
		Menu items allows Upper or Lower case

----------------------------------------
Version: 0.700

Date:	07/04/2026
Author: Jose Luis Gomez Costa

	spindle_control.c:
		RC_SERVO updated for 0-180 deg

----------------------------------------
Version: 0.705

Date:	30/04/2026
Author: Jose Luis Gomez Costa

	pencil.h:
		switched data for GCODE_PENCIL_UP  and GCODE_PENCIL_DOWN
		
----------------------------------------
Version: 1.000

Date:	04/05/2026
Author: Jose Luis Gomez Costa

	First Production version
	
----------------------------------------
Version: 1.100

Date:	06/05/2026
Author: Jose Luis Gomez Costa

	To be corrected: M5 at start/end of GRBL code must send the pencil to UP, not Down
  		spindle_control.c
			Enabled RC_SERVO_INVERT
	
	pencil.h:
		GCODE_PENCIL_DOWN / UP now with M03 movements

----------------------------------------
Version: 1.101

Date:	18/05/2026
Author: Jose Luis Gomez Costa

	For VSCode/PlatformIO

	gcode.h:
		Added declaration for uint8_t gc_execute_line(char *line)

	nuts_bolts.h:
		Corrected warnings for redefinitions max/min/bit

	pencil.c:
		Added address cast fro line_pencil = (char *) &....
	
	spindle_control.c:
		Corrected definition of function :void spindle_set_state(uint8_t state, float rpm)

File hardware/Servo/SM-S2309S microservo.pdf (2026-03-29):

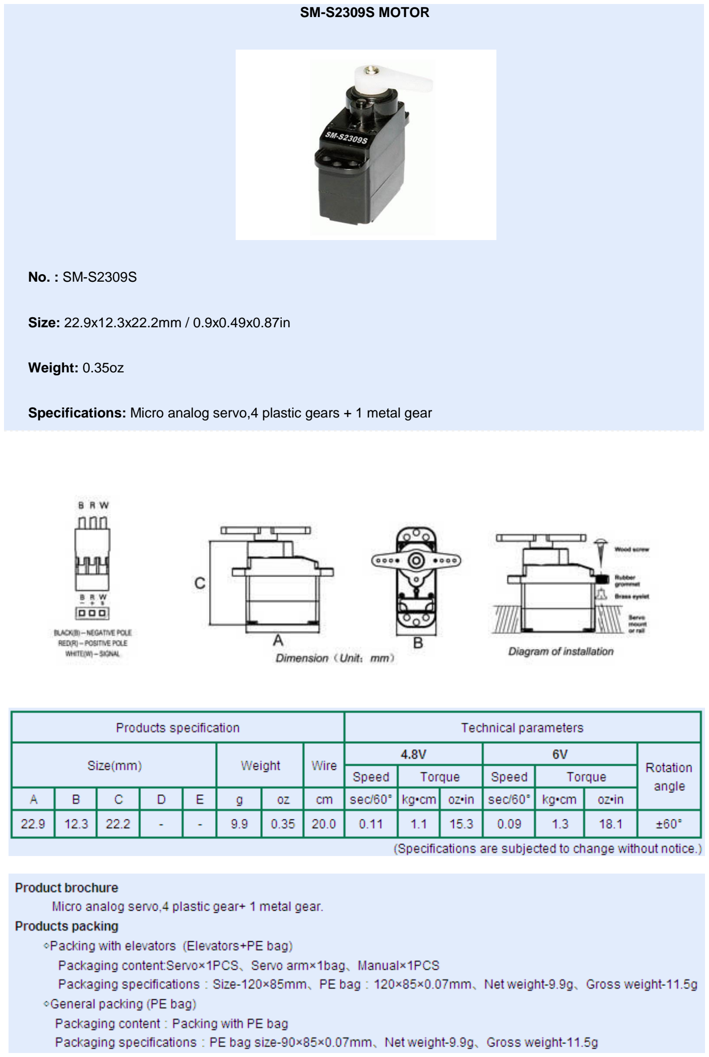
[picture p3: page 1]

SM-S2309S MOTOR

No. : SM-S2309S

Size: 22.9x12.3x22.2mm / 0.9x0.49x0.87in

Weight: 0.35oz

Specifications: Micro analog servo,4 plastic gears + 1 metal gear

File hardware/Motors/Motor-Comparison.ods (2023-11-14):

 | NEMA 17 | RS 5350401 | 42BYGHW609 | 42SHD0001
Step [deg] | 1,8 | 0,9 | 1,8 | 1,8
Hold torque [Ncm] | 28 | 44 | 40 | 26
Current [A] | 1,7 | 1,68 | 1,7 | 0,4
Resistance [Ω] | 1,2 | 1,65 | 2 | 30
Voltage DC [v] | 2,04 | 2,772 | 3,4 | 12
Inductance [mH] | 1,8 | 6,7 | 1,8 | 37
Tao L/R [msec] | 1,500 | 4,061 | 0,900 | 1,233
Diameter shaft [mm] | 5 | 5 | 5 | 5
Leads | 4 | 4 | 4 | 4

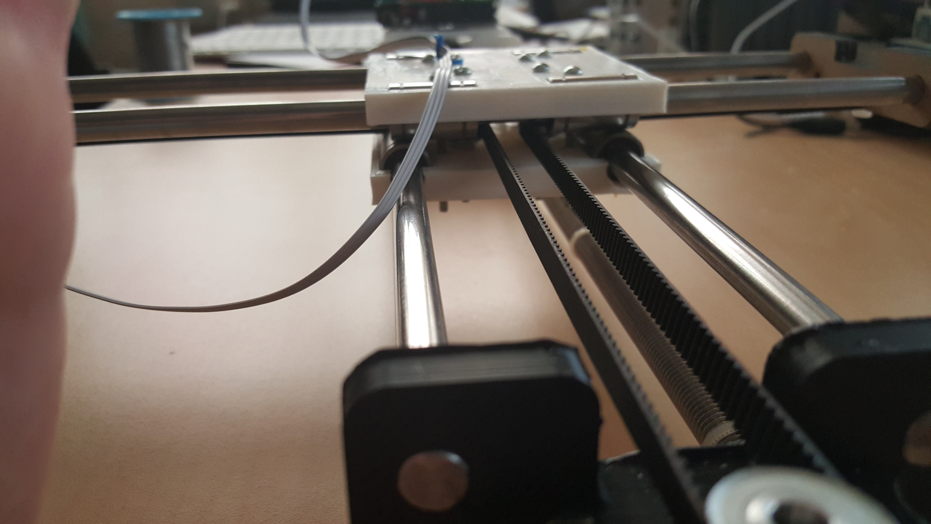
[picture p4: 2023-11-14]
mechanic/docs/Images General/2016-04-03_11.02.12.jpg

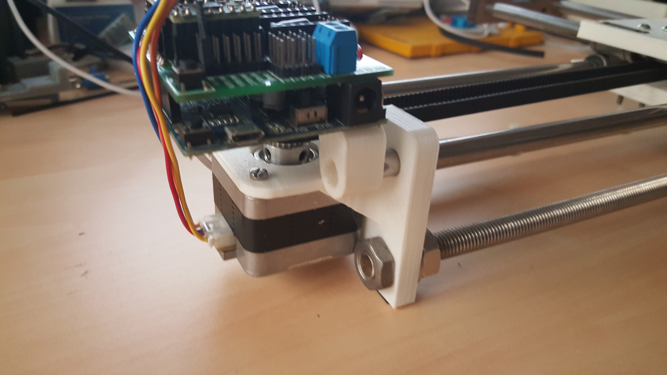
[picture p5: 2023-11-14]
mechanic/docs/Images General/2016-04-03_11.01.58.jpg

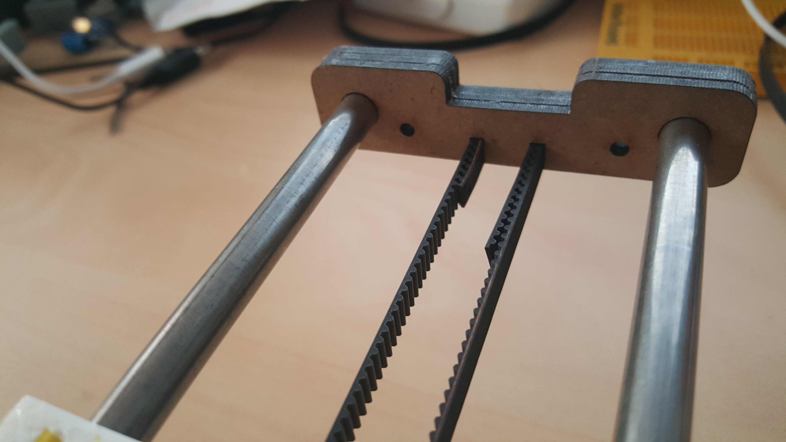
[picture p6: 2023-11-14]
mechanic/docs/Images General/2016-04-03_11.02.22.jpg

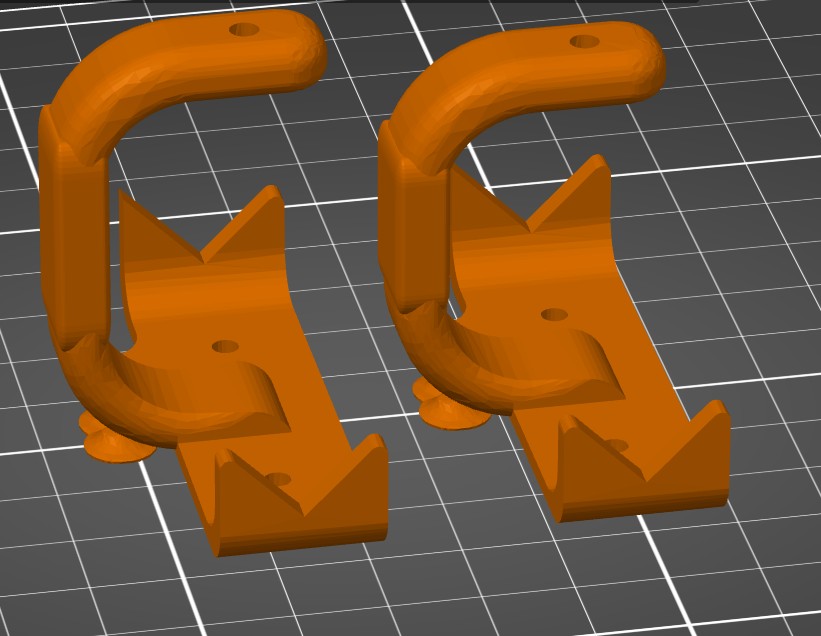
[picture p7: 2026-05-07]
mechanic/Files/Pen_holder/PenHolder_enlarged/PenHolder_both.jpg

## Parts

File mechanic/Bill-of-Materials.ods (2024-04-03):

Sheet: Version
Version | Date | Author | Description
1 | 12/11/23 | Gomez Costa | First Version
2 | 13/11/23 | Gomez Costa | Added sources
3 | 14/11/23 | Gomez Costa | Added Version page
4 | 02/01/24 | Gomez Costa | Added AliExpress cost
https://www.instructables.com/4xiDraw/

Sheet: Composants Electroniques a Acheter
Piece | Qt | Source | Coût |  |  | Coût AliExpress |  |  | Remarques
 |  |  | Unitaire | Devise | Total | Unitaire | Devise | Total
nema 17 steppers (*) Stepper motors should be 40mm or shorter, unless you chose the taller parts that I later created for some users willing to use 48mm tall steppers (like many use for 3D printers). | 2 |  |  |  |  |  |  |  | Existent
micro servo SG90 (plus a 250mm cable extender) | 1 | https://www.fruugoschweiz.com/towerpro-sg90-digital-micro-servo-motor | 20 | CHF | 20 | 4,77 | CHF | 4,77 | Ce servomoteur peut tourner uniquement entre 0 et + 180
Arduino UNO | 1 | https://store.arduino.cc/products/arduino-uno-rev3 | 24 | € | 24 |  |  | 0 | Existent
CNCshield | 1 | https://madeit.ch/boutique/carte-cnc-shield-v3-0/ | 27 | CHF | 27 | 4,91 |  | 4,91 | 1 * plaque de blindage CNC + 4 * DRV8825 pilote de moteur pas à pas + 4 * radiateur + 1 * câble USB
12V 3A power supply | 1 | https://www.distrelec.ch/fr/alimentation-decoupage-industriel-35w-12v-3a-xp-power-lcs35us12 | 14 | CHF | 14 |  |  | 0 | LCS35US12 - Alimentation à découpage, industriel, 35W, 12V, 3A, XP Power
 |  | Total |  |  | 85 | 9,68

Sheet: Composants Mecaniques a Acheter
Piece | Description | Qt | Other | Source | Coût |  |  | Coût AliExpress |  |  | Remarques
 |  |  |  |  | Unitaire | Devise | Total | Unitaire | Devise | Total
8mm smooth rods (400mm long) | Tige lisse | 2 | Leroy-Merlin | https://www.systeal.com/en/linear-guide-on-precision-shaft/1881-2176-smooth-rod-8-mm-diameter.html | 5 | € | 10 | 3,48 | CHF | 6,96 | 500 mm
8mm smooth rods (320mm-long) | Tige | 2 | Leroy-Merlin | https://www.systeal.com/en/linear-guide-on-precision-shaft/1881-2176-smooth-rod-8-mm-diameter.html | 5 | € | 10 | 2,43 | CHF | 4,86
LM8UU | Roulement linéaire | 8 | Aliexpress France | https://madeit.ch/boutique/__trashed/ | 3 | CHF | 24 | 0,8 | CHF | 6,4
20-tooth GT2 pulleys |  | 2 | Aliexpress France | https://www.3dware.ch/GT2-Pulley-20-Teeth-5mm-Bore-En.htm | 3 | CHF | 6 | 0,5 | CHF | 1
F623ZZ bearings | roulements | 10 | Aliexpress France | https://www.3dware.ch/Suche | 1,5 | CHF | 15 | 0,266 | CHF | 2,66
GT2 belt ( 1.4 meters long ) | courroie dentée | 1 | Aliexpress France | https://www.imprimante3dfrance.com/en/checkout/checkout/layout-show | 17 | € | 17 | 3,7 | CHF | 3,7
4mm OD, 100mm-long carbon fiber tubes |  | 2 | Aliexpress France | https://www.clipcarbono.com/en/31-thickness-1mm | 6 | € | 12 | 6,525 | CHF | 13,05
M10 threaded rods (400mm-long each) | Tige filetée | 2 | OK Leroy Merlin | Leroy Merlin | 10 | € | 20 |  |  |  | 1000 mm
30mm M3 screws with nuts |  | 8 |  | Leroy Merlin | 4,5 | € | 4,5 |  |  |  | Qty : 25
16mm M3 screws with nuts |  | 4 |  | Leroy Merlin | 4,5 | € | 4,5 |  |  |  | Qty : 30
6mm M3 screws |  | 8 |  | Leroy Merlin | 2,5 | € | 5 |  |  |  | Qty : 5
15mm M3 screws |  | 2 |  | Leroy Merlin |  | € | 0 |  |  |  | Use 16mm
M10 nuts |  | 8 |  | Leroy Merlin | 3 | € | 3
M3 washers |  | 4 |  | Leroy Merlin | 4 | € | 4
 |  |  |  | Total |  |  | 135 | 38,63

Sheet: Composants Mecaniques a Imprimer
Element | Fichier stl | Photo
Arduino_grip | DrawingMachine_-_Arduino_grip.stl | 3cb0abeb9d214008fc2388d2e4c91a41.png
base | DrawingMachine_-_base.stl | 6c0ed874e7cd5bdfad3f3c4ed5c44fe5.png
base_with_nuts | DrawingMachine_-_base_with_nuts.stl | 15ffc615c08a940bccb83b55fc7a99e2.png
newEndX_1 | DrawingMachine_-_newEndX_1.stl | 8ec31fd9d4210ecdafe3e3a3456fbaff.png
Pen_Carriage_1 | DrawingMachine_-_Pen_Carriage_1.stl | e21e8bd9d29e930654758aaa403c2874.png
Pen_holder_1 | DrawingMachine_-_Pen_holder_1.stl | db50cb72c5c095c3608d31412b09bc57.png
servoHolder | DrawingMachine_-_servoHolder.stl | 42fe427f1709701ea06472a32bfd8e30.png
EndY | EndY.stl | b316fb4817062c72a014752c5b8d428e.png
EndY2 | EndY2.stl | a6f320b1239115a57c8a32e8a086a5a2.png
newEnd40x20_1 | newEnd40x20_1.stl | newEnd40x20_1.png
Taller_Arduino_support | Taller_Arduino_support.stl | 9923291e9934ea50db126e92308204f9.png
tensor | tensor.stl | 8265fb9e76ecd02bc4b425174508b961.png

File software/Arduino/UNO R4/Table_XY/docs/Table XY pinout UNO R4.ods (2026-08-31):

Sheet: Interfaces
UNO R4 R7FA4M1AB3CFM#AA0 LQFP64 bits
# | Description
8 | PWM Timers (2 * 32bits / 6 * 16bits)
2
1
8
1 | ADC 14 Bits
4
2
1
2 | Analog Comparator 8 bits
1
2
1 | DAC 12 bits

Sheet: Analog connector
JANALOG
Arduino |  |  | GRBL |  |  |  |  |  | CPU
Pin | Function | Type | Direction | Pull-Up | Interrupt on change | PWM | Description | Hardware | PORTx | Pin (Pxx) | Interrupt on change | PWM capable | Pull-Up | Periferal
1 | see below | see below |  |  |  |  |  |  | 2 / ? | 201 / ESP32-S3
2 | IOREF | connected to +5v
3 | Reset | Reset
4 | +3V3 Power Rail | +3V3
5 | +5V Power Rail | +5V
6 | Ground | GND
7 | Ground | GND
8 | DC Input : VIN pad / DC Jack | VIN
9 | Analog0 / GPIO | A0 | In | yes | yes |  | Control : Abort (1) | Push button | 0 | 14 | no |  | yes | GPIO
10 | Analog1 / GPIO | A1 | In | yes | yes |  | Control : Feed Hold | Push button | 0 | 0 | yes |  | yes | GPIO
 |  |  |  |  |  |  | Control : Safety Door | selectable
11 | Analog2 / GPIO | A2 | In | yes | yes |  | Control : Resume (2) | Push button | 0 | 1 | yes |  | yes | GPIO
12 | Analog3 / GPIO | A3 | Out |  |  |  | Coolant Enable |  | 0 | 2 |  |  |  | GPIO
13 | Analog4 / GPIO | A4 / SDA | Out |  |  |  | Coolant Mist | selectable | 1 | 101 |  |  |  | GPIO
 |  |  | Out |  |  |  | Test 1 | Test Point
14 | Analog5 / GPIO | A5 / SCL | In | Selectable |  |  | Probe | Not used | 1 | 100 |  |  |  | GPIO
 |  |  | Out |  |  |  | Test 2 | Test Point
 |  |  | Notes
 |  |  | all | CONTROLs pins must be on the same port and not on a port with other input pins |  |  |  |  | CONTROL pins : NOT all IRQ-capable
 |  |  | (1) | In cpu_map_atmega328p.h, named : RESET_BIT |  |  |  |  | CONTROL pins : must be checked through a Timer interrupt
 |  |  | (2) | In cpu_map_atmega328p.h, named : CYCLE_START_BIT
Arduino | CPU
Pin | Function
1 | MD : Mode BOOT

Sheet: Digital connector
JDIGITAL
Arduino |  |  | GRBL |  |  |  |  |  | CPU
Pin | Function | Type | Direction | Pull-Up | Interrupt on bit change | PWM | Description for GRBL | Hardware | PORTx | CPU (Pxx) | Interrupt on bit change | PWM capable | Periferal | Remarques
1 | D0 | Digital / GPIO |  |  |  |  |  |  | 3 | 301 |  |  | SCI2 RXD | While in MODE_DEBUG, SCI2 is Serial Port for GRBL operations, SCI9 is Debugging port
2 | D1 | Digital / GPIO |  |  |  |  |  |  | 3 | 302 |  |  | SCI2 TXD
3 | D2 | Digital / GPIO | Out |  | - | no | Step Pulse X-Axis | Pololu Step X | 1 | 104 |  |  | GPIO
4 | D3 | Digital / GPIO | Out |  | - | no | Step Pulse Y-Axis | Pololu Step Y | 1 | 105 |  |  | GPIO
5 | D4 | Digital / GPIO | Out |  | - | no | Step Pulse Z-Axis | Pololu Step Z | 1 | 106 |  |  | GPIO
6 | D5 | Digital / GPIO | Out |  | - | no | Direction Pulse X-Axis | Pololu Dir X | 1 | 107 |  |  | GPIO
7 | D6 | Digital / GPIO | Out |  | - | no | Direction Pulse Y-Axis | Pololu Dir Y | 1 | 111 |  |  | GPIO
8 | D7 | Digital / GPIO | Out |  | - | no | Direction Pulse Z-Axis | Pololu Dir Z | 1 | 112 |  |  | GPIO
9 | D8 | Digital / GPIO | Out |  | - | no | Stepper Enable/Disable | Pololu Enable X-Y | 3 | 304 |  |  | GPIO
10 | D9 | Digital / GPIO | In | yes | yes | - | Limit X-Axis | Limit switch | 3 | 303 | no |  | GPIO
11 | D10 | Digital | In | yes | yes | - | Limit Y-Axis | Limit switch | 1 | 103 | yes : kr03 |  | GPIO
12 | D11 | Digital | Out |  | - | yes | Servo control : Pencil control | Servo | 4 | 411 |  | yes | GPT6_A
13 | D12 | Digital | In | yes |  | - | Limit Z-Axis | open | 4 | 410 | yes |  | GPIO
14 | D13 | Digital | Out |  |  |  | Test 3 | Test Point | 1 | 102 |  |  | GPIO
15 | GND | Power
16 | AREF | Analog Reference |  |  |  |  |  |  | 0 | 10
17 | A4 / SD4 | Digital |  |  |  |  |  |  | Defined in Analog connector page
18 | A5 / SD5 | Digital
 |  |  | LIMIT pins must be on the same port and not on a port with other input pins (Control). |  |  |  |  |  | LIMIT pins : NOT in the same port and NOT all IRQ-capable
 |  |  | PULSE DIRECTION pins must be on the same port |  |  |  |  |  | LIMIT pins : must be checked through a Timer interrupt
 |  |  | PULSE SET pins must be on the same port
 |  |  |  |  |  |  |  |  | PULSE DIRECTION pins on the same port
 |  |  |  |  |  |  |  |  | PULSE SET pins on the same port

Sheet: E-Stop
E-Stop
Connected to RST button in CNC Shield

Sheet: LEDs
LEDs
 | CPU
Function | Pin (Pxx) | PORTx
Built In | 102 | 1
TX | 109 | 1
RX | GPIO 43 (ESP32-S3)

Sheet: Servo Measurement
 | R3 | R4
Frequency | 60 | 50 | Hz
M5 pulse | 2,55 | 2 | msec
M03S85 pulse | 700 | 1530 | usec | GCODE_PENCIL_DOWN
M03S00 pulse | 2,56 | 2 | msec | GCODE_PENCIL_UP
Version |  | R4 GRBL 0.952

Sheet: Serial-to-USB
 | CPU
Function | Pin (Pxx) | Peripheral | ESP J6 pin # [3v3] | Description
Receive from PC via USB | 110 | SCI9 | 3 | RXD from ESP
Transmit to PC via USB | 109 | SCI9 | 5 | TXD to ESP
Parameter | Value
Baud rate | 115200
Data bits | 8
Stop bits | 1
Parity | No
XON-XOFF | Default disabled
BRR / MDDR for Clock calculations. See page 726 of Renesas RA4M1 Group User’s Manual: Hardware
PCLKA | 48 | MHz
BGDM | 0
ABCS | 0
ABCSE | 0
n | 0
M (MDDR) | 236
N (BRR) | 11
Error | 0,030 | %

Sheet: Flash Access
Event | Time [msec] | Conditions
Read | 0,350 | 1024 bytes
Erase | 6,000 | 1024 bytes
Blanck check | 0,500 | 1024 bytes
Write | 45,000 | 1024 bytes
Status check | 0,001 | -
Total | 51,850 | Write + Read

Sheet: Clocks
Clock | Division Initial setting | Peripheral
PCLKA | 1 | High speed peripheral bus
PCLKB | 2 | Peripheral bus
PCLKC | 1 | ADC14
PCLKD | 1 | GPT
ICK | 1 | CPU, DTC, DMAC, Flash SRAM
FCK | 2 | Flash Interface clock
ICLK ≥ PCLKA ≥ PCLKB
PCLKD ≥ PCLKA ≥ PCLKB
ICLK ≥ FCLKA

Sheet: IELSR list
Condition | IELSRn | Value | Use | Peripheral | Function
Test : Serial + LED Matrix | 0 | 0x1E | AGT0_AGTI | AGT Timer 0 | Millisecond count
 | 1 | 0x7D | GPT4_OVF | GPT PWM Timer 4 | LED Matrix control
 | 2 | 0xA9 | SCI9_TXI | SCI 9 | Serial Port
 | 3 | 0xAA | SCI9_TEI | SCI 9
 | 4 | 0xA8 | SCI9_RXI | SCI 9
 | 5 | 0xAB | SCI9_ERI | SCI 9
Test : Serial | 0 | 0x1E | AGT0_AGTI | AGT Timer 0 | Millisecond count
 | 1 | 0xA9 | SCI9_TXI | SCI 9 | Serial Port
 | 2 | 0xAA | SCI9_TEI | SCI 9
 | 3 | 0xA8 | SCI9_RXI | SCI 9
 | 4 | 0xAB | SCI9_ERI | SCI 9
AGT1 (AGT Timer 1) | 20 | 0x21 | AGT1_AGTI | AGT Timer 1 | Limits and Buttons status check
GPT320 (Timer 0 32 bits) | 21 | 0x5D | GPT0_OVF | GPT Overflow | Main Interruption routine
AGT1 | 22 | 0x57 | GPT0_CCMPA | GPT Compare match A | End of Direction-to-Step pulse delay (if enabled)
AGT1 | 23 | 0x58 | GPT0_CCMPB | GPT Compare match B | End of Step pulse high value
Serial SCI9 | 24 | 0xA9 | SCI9_TXI | Free to Transmit | Serial Port for communication with PC via USB
 | 25 | 0xA8 | SCI9_RXI | Data received

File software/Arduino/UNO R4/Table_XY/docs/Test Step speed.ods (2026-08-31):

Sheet: Test
CPU | Test | X / Y
 |  | 10000 / 15000 | 10000 / 15000 | -10000 / 20000 | -10000 / 20000 | Conditions
R3 | Speed | 50 | 100 | 50 | 100 | All normal for R3
#Pulse Y per Pulse X | #Pulse Y per Pulse X | 1 / 5 | 1 / 5 | 3 / 1 | 3 / 1
Period X [usec] | Period X [usec] | 5000 | 2400 | 17400 | 7500
Period Y [usec] | Period Y [usec] | 25000 | 12000 | 5800 | 2500
Interruption Period [usec] | Interruption Period [usec] | 625 | 280 | 670 | 312
#Interruptions per Pulse Y | #Interruptions per Pulse X | 8 | 8 | 24 | 24
 | #Interruptions per Pulse Y | 40 | 40 | 8 | 8
Length Interruption [usec] | Length Interruption [usec] | 15 | 18 | 15 | 15
R4 | Speed | 50 | 100 | 50 | 100 | AMASS_LEVELx R3 %3
 | #Pulse Y per Pulse X | 1/5 | 1/5 | 3/1 | 3/1
 | Period X [usec] | 26000 | 11480 | 80000 | 35700
 | Period Y [usec] | 130000 | 58000 | 26740 | 11700
 | Interruption Period [usec] | 3330 | 1500 | 3330 | 1450
 | #Interruptions per Pulse X | 8 | 8 | 24 | 24
 | #Interruptions per Pulse Y | 40 | 40 | 8 | 8
 | Length Interruption [usec] | 4 | 6 | 4-6 | 4-6
 | Difference Period X R4/R3 | 5,2 | 4,8 | 4,6 | 4,8
 | Difference Period Y R4/R3 | 5,2 | 4,8 | 4,6 | 4,7
 | Difference Main ISR R4/R3 | 5,3 | 5,4 | 5,0 | 4,6
 | Speed | 50 | 100 | 50 | 100 | AMASS_LEVELx R3 *3 / cycle value multiplied by 0,2
 | #Pulse Y per Pulse X | 1 / 5 | 1 / 5 | 3 / 1 | 3 / 1
 | Period X [usec] | 5150 | 2400 | 16500 | 7250 | prep_segment->cycles_per_tick = cycles * 0.2
 | Period Y [usec] | 26000 | 11700 | 5555 | 2400
 | Interruption Period [usec] | 670 | 286 | 670 | 300
 | #Interruptions per Pulse X | 8 | 8 | 24 | 24
 | #Interruptions per Pulse Y | 40 | 40 | 8 | 8
 | Length Interruption [usec] | 4 to 6 | 4 to 6 | 4 to 6 | 4 to 6
 | Difference Period X R4/R3 | 1,03 | 1,00 | 0,95 | 0,97
 | Difference Period Y R4/R3 | 1,04 | 0,98 | 0,96 | 0,96
 | Difference Main ISR R4/R3 | 1,07 | 1,02 | 1,00 | 0,96

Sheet: Waves
 | 10000/15000 F50
R3
R4
 | 10000/15000 F100
R3
R4
 | -10000/20000 F50
R3
R4
 | -10000/20000 F100
R3
R4
 | X 10000 F100
R3
R4

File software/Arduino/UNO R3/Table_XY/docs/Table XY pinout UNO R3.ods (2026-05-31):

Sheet: Interfaces
UNO R3 ATmegaA328P
Interface | # | Description
Timer 16 bits | 3 | Timers (2 * 8bits / 1 * 16bits)
RealTime counter | 1
PWM channel | 6
ADC channels | 6 | ADC 10 bit. PDIP package
Serial USART | 1
SPI Interface | 1
WD Timer | 1
Analog comparator | 1 | On chip
Interrupt and Wake Up on pin change | 1
I2C | 1

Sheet: Analog connector
JANALOG
Arduino |  |  | GRBL |  |  |  |  |  | CPU
Pin | Function | Type | Direction | Pull-Up | Interrupt on change | PWM | Description | Hardware | CPU | Bit | PWM | Periferal
1 | see | see
2 | IOREF | connected to +5v
3 | Reset | Reset |  |  |  |  |  |  | C | 6
4 | +3V3 Power Rail | +3V3
5 | +5V Power Rail | +5V
6 | Ground | GND
7 | Ground | GND
8 | DC Input : VIN pad / DC Jack | VIN
9 | Analog0 / GPIO | A0 | In | yes | yes |  | Control : Abort (1) | Push button | C | 0 | - | GPIO
10 | Analog1 / GPIO | A1 | In | yes | yes |  | Control : Feed Hold | Push button | C | 1 | - | GPIO
11 | Analog2 / GPIO | A2 | In | yes | yes |  | Control : Resume (2) | Push button | C | 2 | - | GPIO
12 | Analog3 / GPIO | A3 | Out |  |  |  | Coolant Enable |  | C | 3 | no
13 | Analog4 / GPIO | A4 / SDA | Out |  |  |  | ISR Test | Test Point | C | 4 | no | GPIO
14 | Analog5 / GPIO | A5 / SCL |  |  |  |  | not used (reserved) |  | C | 5
 |  |  | Notes
 |  |  | all | CONTROLs pins must be on the same port and not on a port with other input pins
 |  |  | (1) | In cpu_map_atmega328p.h, named : RESET_BIT
 |  |  | (2) | In cpu_map_atmega328p.h, named : CYCLE_START_BIT
Arduino | CPU
Pin | Function
1 | not connected

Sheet: Digital connector
JDIGITAL
Arduino |  |  | GRBL |  |  |  |  |  | CPU
Pin | Function | Type | Direction | Pull-Up | Interrupt on bit change | PWM | Description for GRBL | Hardware | CPU | Bit | Interrupt on bit change | PWM | Periferal
1 | D0 | Digital / GPIO |  |  |  |  |  |  | D | 0
2 | D1 | Digital / GPIO |  |  |  |  |  |  | D | 1
3 | D2 | Digital / GPIO | Out |  | - | no | Step Pulse X-Axis | Pololu Step X | D | 2 | - |  | GPIO / Timer 0 / 1
4 | D3 | Digital / GPIO | Out |  | - | no | Step Pulse Y-Axis | Pololu Step Y | D | 3 | - |  | GPIO / Timer 0 / 1
5 | D4 | Digital / GPIO | Out |  | - | no | Step Pulse Z-Axis | Pololu Step Z | D | 4 | - |  | GPIO / Timer 0 / 1
6 | D5 | Digital / GPIO | Out |  | - | no | Direction Pulse X-Axis | Pololu Dir X | D | 5 | - |  | GPIO / Timer 0 / 1
7 | D6 | Digital / GPIO | Out |  | - | no | Direction Pulse Y-Axis | Pololu Dir Y | D | 6 | - |  | GPIO / Timer 0 / 1
8 | D7 | Digital / GPIO | Out |  | - | no | Direction Pulse Z-Axis | Pololu Dir Z | D | 7 | - |  | GPIO / Timer 0 / 1
9 | D8 | Digital / GPIO | Out |  | - | no | Stepper Enable/Disable | Pololu Enable X-Y | B | 0 | - |  | GPIO
10 | D9 | Digital / GPIO | In | yes | yes | - | Limit X-Axis | Limit switch | B | 1 | yes | - | GPIO
11 | D10 | Digital | In | yes | yes | - | Limit Y-Axis | Limit switch | B | 2 | yes | - | GPIO
12 | D11 | Digital | Out |  | - | yes | Servo control : Pencil control | Servo | B | 3 | - | yes | TCCR2
13 | D12 | Digital | In | yes |  | - | Limit Z-Axis | open | B | 4 | yes | - | GPIO
14 | D13 | Digital |  |  |  |  | Not used |  | B | 5
15 | GND | Power
16 | AREF | Analog Reference
17 | A4 / SD4 | Digital |  |  |  |  |  |  | Defined in Analog connector page
18 | A5 / SD5 | Digital
 |  |  | LIMIT pins must be on the same port and not on a port with other input pins (Control).
 |  |  | PULSE DIRECTION pins must be on the same port
 |  |  | PULSE SET pins must be on the same port

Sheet: E-Stop
E-Stop
Connected to RST button in CNC Shield

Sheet: LEDs
LEDs
 | CPU
Function | Pin (Pxx) | PORTx
Built In | B | 5
TX | ATMEGA16U2-MU(R) D | 5
RX | ATMEGA16U2-MU(R) D | 4

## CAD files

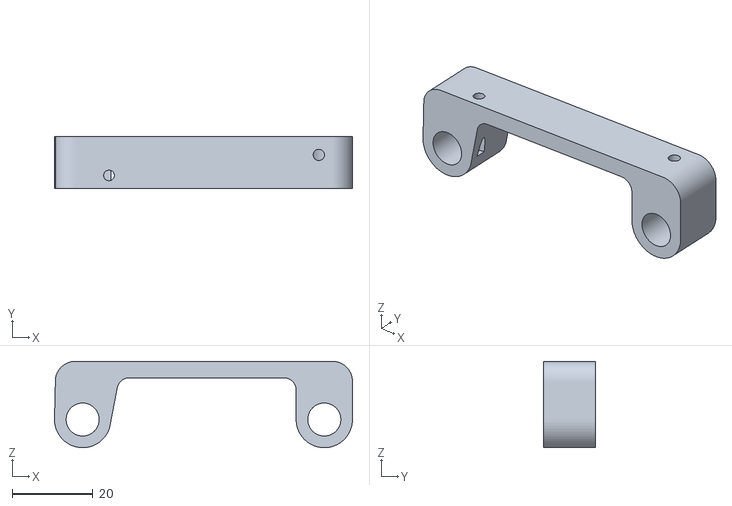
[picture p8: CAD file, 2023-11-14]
mechanic/Files/Arduino Grip/DrawingMachine_-_Arduino_grip.stl
74.0 x 13.0 x 21.5

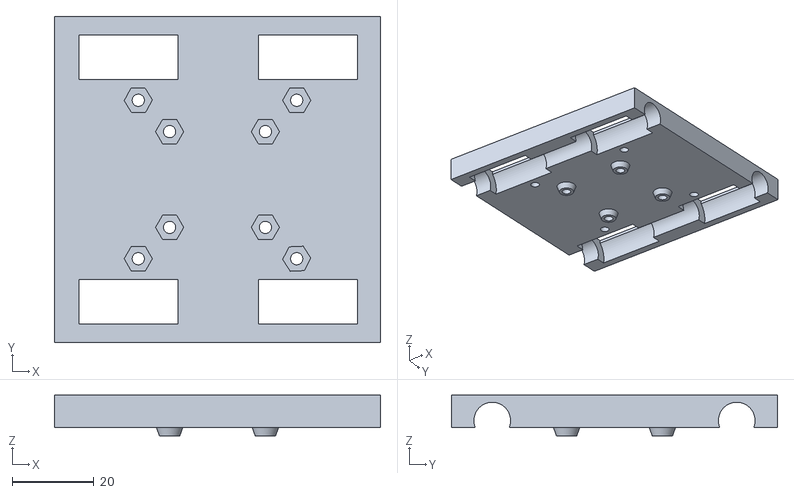
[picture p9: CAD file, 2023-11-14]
mechanic/Files/base with nuts/DrawingMachine_-_base_with_nuts.stl
80.0 x 80.0 x 10.0

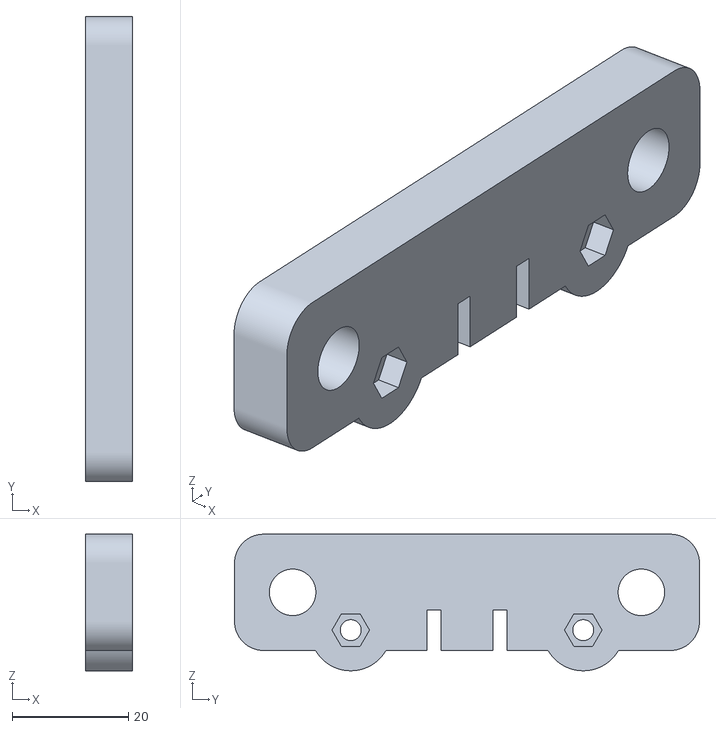
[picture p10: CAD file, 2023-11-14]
mechanic/Files/End Y 2/EndY2.stl
8.00 x 80.0 x 23.5

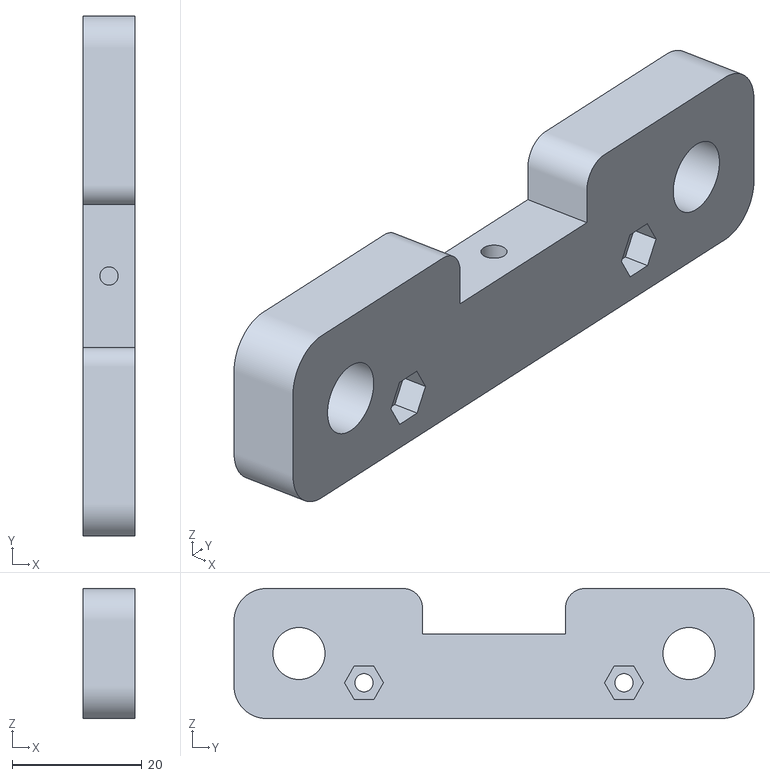
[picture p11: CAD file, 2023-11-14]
mechanic/Files/End Y/EndY.stl
8.00 x 80.0 x 20.0

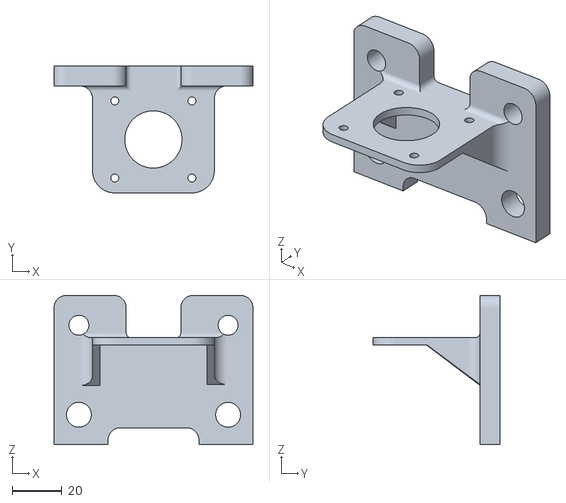
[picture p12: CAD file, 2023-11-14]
mechanic/Files/New EndX/DrawingMachine_-_newEndX_1.stl
80.0 x 51.0 x 60.0

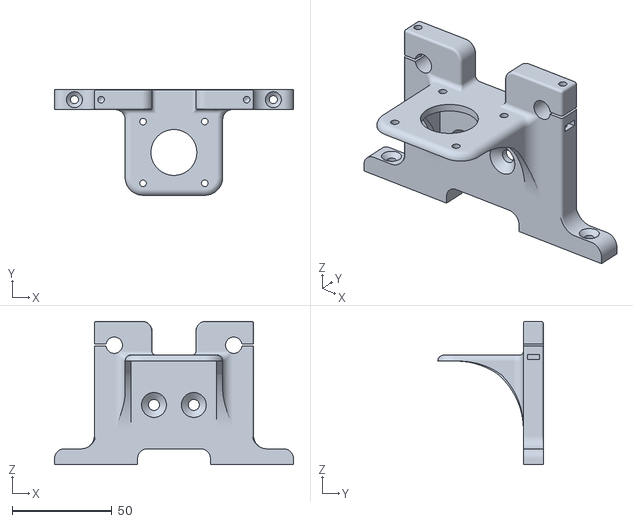
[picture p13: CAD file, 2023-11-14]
mechanic/Files/newEnd40x20_1/newEnd40x20_1.stl
120.0 x 53.0 x 72.0

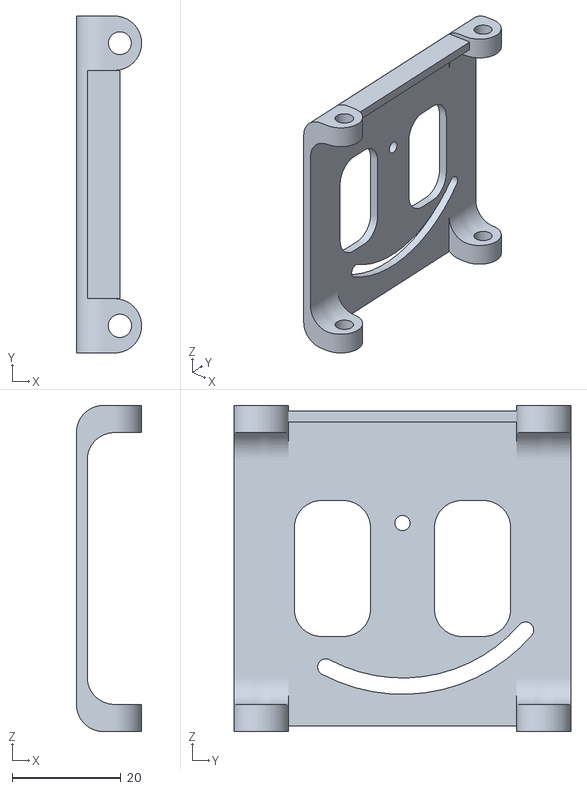
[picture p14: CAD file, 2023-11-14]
mechanic/Files/Pen_Carriage_1/DrawingMachine_-_Pen_Carriage_1.stl
12.0 x 62.0 x 60.0

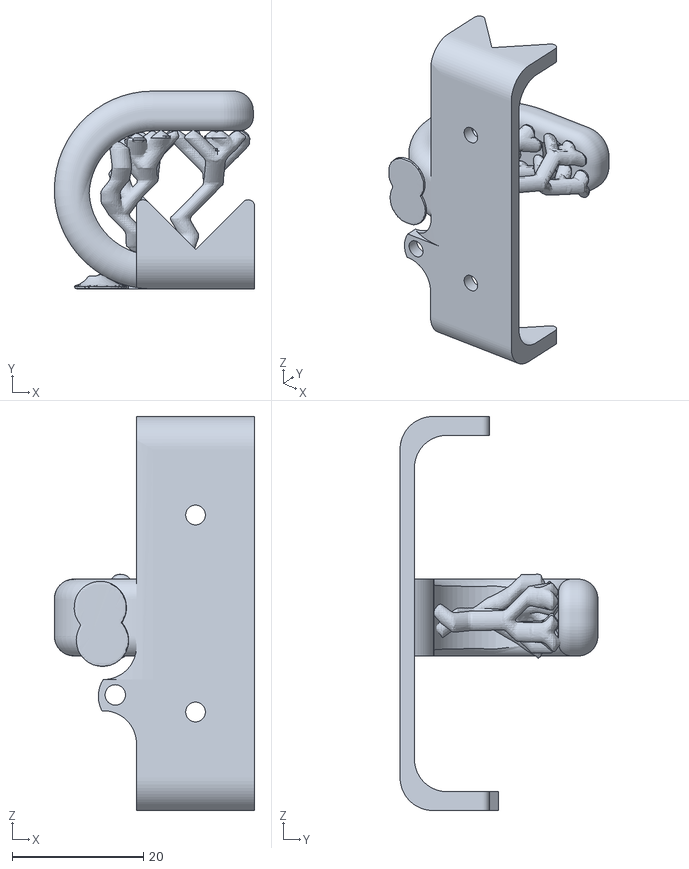
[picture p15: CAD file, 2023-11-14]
mechanic/Files/Pen_holder/DrawingMachine_-_Pen_holder_1.stl
30.5 x 30.1 x 60.0

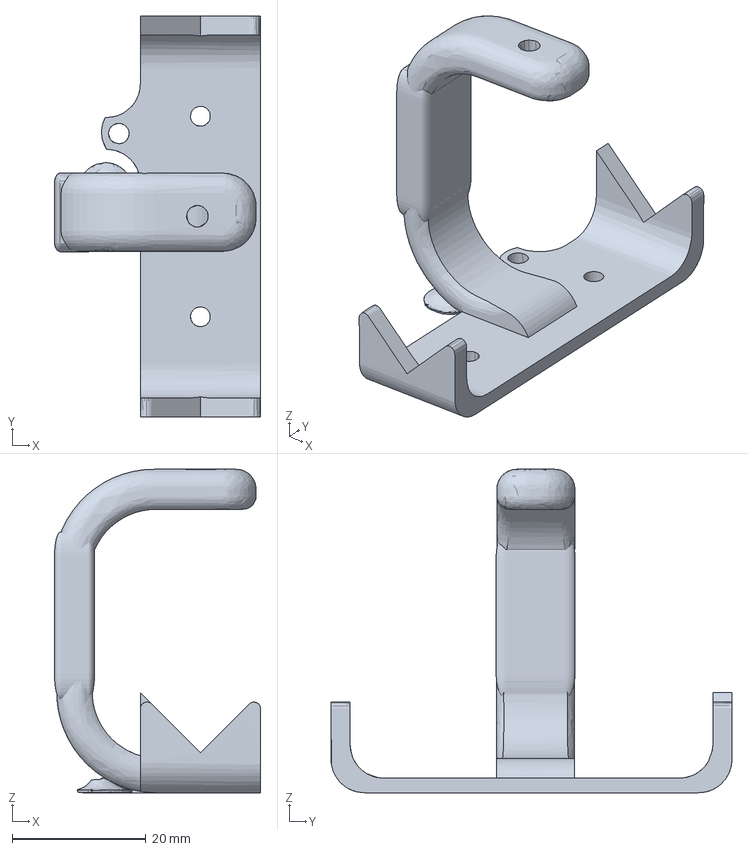
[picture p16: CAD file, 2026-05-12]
mechanic/Files/Pen_holder/PenHolder_enlarged/PenHolder_enlarged_long.3mf
30.8 x 60.0 x 48.4 mm

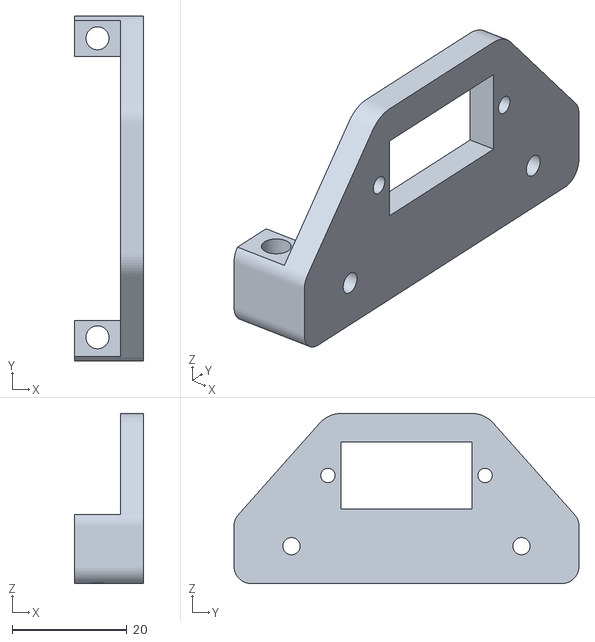
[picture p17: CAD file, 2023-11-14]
mechanic/Files/servo Holder/DrawingMachine_-_servoHolder.stl
12.0 x 60.0 x 29.6

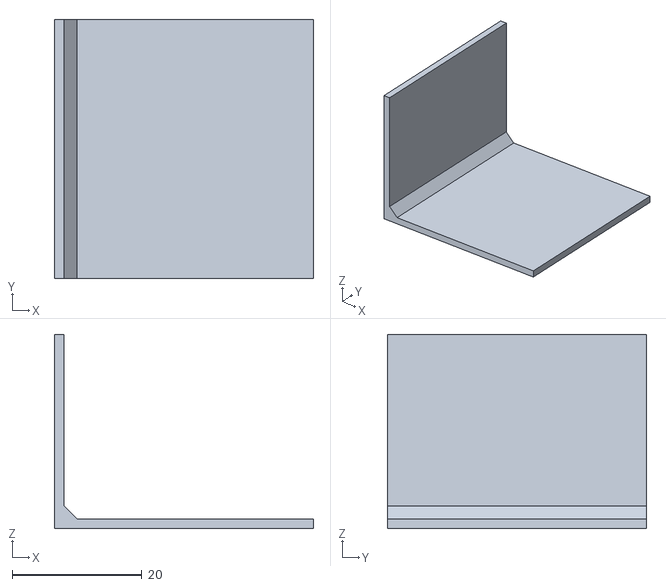
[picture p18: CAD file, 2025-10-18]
mechanic/Files/Support_LimitSwitchFilterCard/Support_LimitSwitchFilterCard.stl
40.0 x 40.0 x 30.0

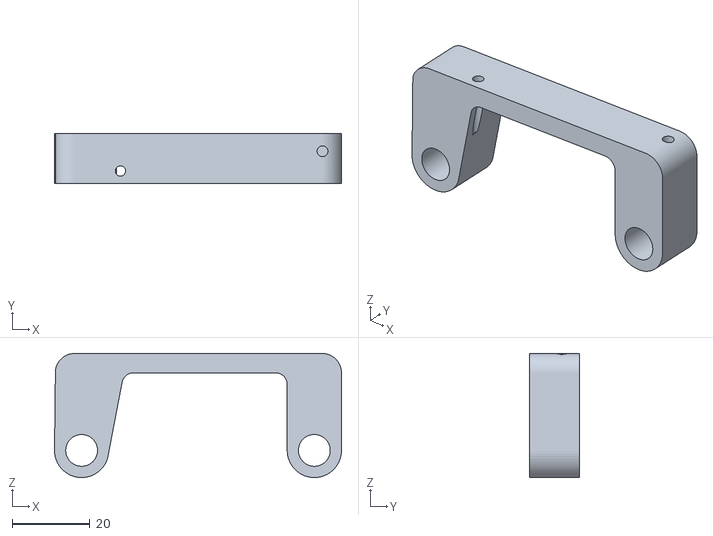
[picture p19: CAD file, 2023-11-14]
mechanic/Files/Taller_Arduino_support/Taller_Arduino_support.stl
74.0 x 13.0 x 32.0

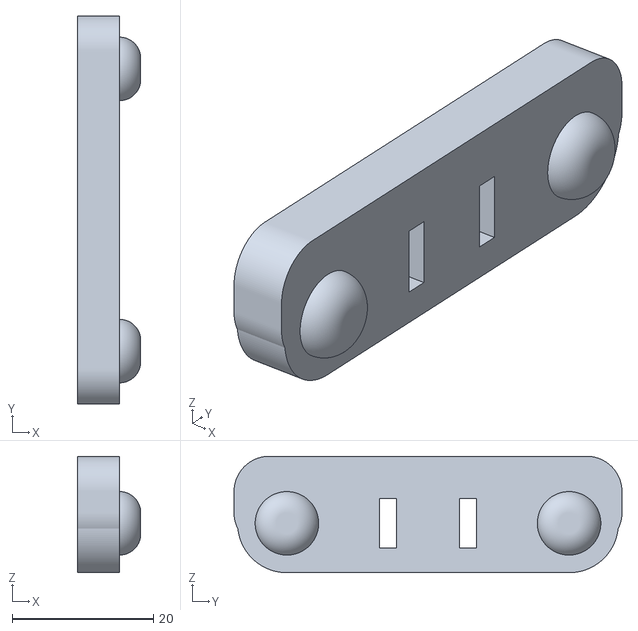
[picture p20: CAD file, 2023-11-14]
mechanic/Files/tensor/tensor.stl
9.00 x 55.0 x 16.5

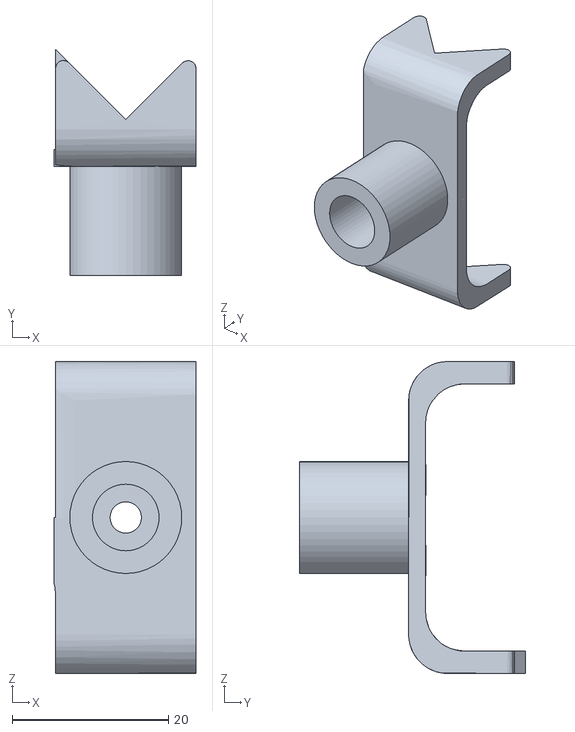
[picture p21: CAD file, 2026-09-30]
mechanic/Printer3D-Prusa/PenHolder_inverse/PenHolder_inverse_enlarged.stl
18.2 x 29.0 x 40.0

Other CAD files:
mechanic/Files/base/DrawingMachine_-_base.stl
mechanic/Printer3D-Prusa/PenHolder_enlarged/PenHolder_enlarged.3mf
mechanic/Printer3D-Prusa/Servo_holder/Servo_holder.3mf
mechanic/Printer3D-Prusa/Support_LimitSwitch/Support_LimitSwitch_FilterCard.3mf
mechanic/Files/PenHolder_inverse/PenHolder_inverse.3mf
mechanic/Files/Pen_holder/PenHolder_enlarged/PenHolder_base.stl
mechanic/Files/Pen_holder/PenHolder_enlarged/PenHolder_enlarged_3mm.stl
mechanic/Files/Pen_holder/PenHolder_enlarged/PenHolder_enlarged_4mm.stl
mechanic/Files/Pen_holder/PenHolder_enlarged/PenHolder_enlarged_both.3mf
mechanic/Files/Pen_holder/PenHolder_enlarged/PenHolder_enlarged_both.stl
mechanic/Files/Pen_holder/PenHolder_enlarged/PenHolder_enlarged_small.3mf
mechanic/Files/Pen_holder/PenHolder_enlarged/PenHolder_tour.stl
mechanic/Printer3D-Prusa/PenHolder_inverse/PenHolder_inverse.3mf
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

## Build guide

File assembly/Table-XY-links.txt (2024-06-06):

https://www.instructables.com/4xiDraw/
Pièces en CAD-3D: https://cad.onshape.com/documents/236f46681d1cbe31f6d52db0/w/5948c0b4f86507971afed68c/e/97c3b5c3e30764b62f7eb951

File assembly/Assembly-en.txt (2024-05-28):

I recommend the following building sequence:

- Slide two LM8UU in each of the two longest smooth rods.
	
- Slide the rods into the motor pieces, one on each side (leave an extra 20mm of the rods in one of the two sides protruding from the part towards the motor, this will later be used for supporting the Arduino holder).
    
- Insert the M10 threaded rods so each one supports one side of the motor-supporting pieces using a nut on each side (total 8 M10 nuts).

- Mount the nema 17 stepper motors on the two big plastic parts using 8 M3 screws (8mm long).
    
- Insert 8 M3 nuts into the nut-holders in the bottom squared carriage and place it supporting the LM8UU linear bearings you inserted in the long smooth rods already installed.
    
- Take the remaining (shorter) two smooth rods and insert two LM8UU linear bearings on each one of them.
    
- Insert the two endY parts on each end of the pair of smooth rods. Now you have the second axis done.
    
- Insert the top square carriage over the 4 linear bearings of the shorter smooth rods.
    
- Insert 4 M30 30mm-long screws in the 4 central holes of the top square carriage, put the carriage upside-down carefully so the head of the screws will lay on the table and the screws will point upward.
    
- Insert one F623ZZ bearing with the flange down, next an M3 washer and finally another bearing but now with the flange up) into each one of the four screws of the top square carriage.
    
- Use a post-it or a similar-size piece of paper to press it against each one of the screws protruding so paper is perforated and is pressing against the top of the bearings. The goal is for this paper to hold them in place while we put the whole thing upside-down preventing the bearings to fall off.
    
- Place the top carriage over the bottom carriage so the smooth rods on the top form a right angle with the bottom smooth rods.
    
- Screw lightly each one of the four M3 screws and once you notice each one is attached to the nut in the bottom tear the post-it paper apart. Next finish tightening the screws and add the other 4 M3 30mm screws that do not have a bearing but add strength to the union of top and bottom parts of the carriage.
    
- Place one GT2 pulley on each stepper motor but do not tighten the grub bolt yet.
    
- Place a pair of F623ZZ bearings with an M3 washer in between fixed with an M3 screw in the end Y part that will support the servo part.
    
- Insert the belt all along its path (the crossings of the central carriage are a bit tricky). And once pulleys are aligned with the belt tighten the grub screws on each one.

- Use two M3 screws and two nuts to attach the servo support part and later add the microsevo using the two screws that come with it.

- Make sure the vertical two holes in the servo support part are 4mm diameter and that the carbon fiber tubes can be inserted into them (if not, drill the holes with a 4mm drill bit). Insert both tubes from the top but only mid way. And next insert from the top the vertical carriage (the one that looks like a smiling face). Gently push it down till you can insert the remaining half of the carbon fiber tubes so they are inserted into the bottom holes of this carriage.

- Using a couple of M3 screws and nuts fix the pen-holder part to the vertical carriage.

- Push the Arduino holder into the protruding smooth rods on one of the stepper motor holders. Use a couple of M3 screws to attach the Arduino board to the plastic holder.

Bill of materials

- 4 8mm smooth rods (two 400mm-long and two 320mm-long)
- 8 LM8UU
- 2 20-tooth GT2 pulleys
- 10 F623ZZ bearings
- 1 GT2 belt ( 1.4 meters long )
- 2 M10 threaded rods (400mm-long each)
- 8 M10 nuts
- 8 30mm M3 screws with nuts
- 8 6mm M3 screws
- 4 16mm M3 screws with nuts
- 4 M3 washers
- 2 4mm OD, 100mm-long carbon fiber tubes
- 2 15mm M3 screws

Electronics
- 2 nema 17 steppers (*)
- 1 micro servo SG90 (plus a 250mm cable extender)
- 1 Arduino UNO
- 1 CNCshield
- 2 Pololu stepsticks
- 1 12V 2A power supply
- 1 USB cable

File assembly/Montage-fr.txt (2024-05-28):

Montage

Je recommande la séquence de construction suivante :

- Glissez deux LM8UU dans chacune des deux tiges lisses les plus longues.

- Glissez les tiges dans les pièces du moteur, une de chaque côté (laissez 20 mm supplémentaires de tiges dans l'un des deux côtés dépassant de la pièce vers le moteur, cela servira plus tard pour supporter le support Arduino).

- Insérez les tiges filetées M10 de manière à ce que chacune supporte un côté des pièces de support du moteur à l'aide d'un écrou de chaque côté (total 8 écrous M10).

- Montez les moteurs pas à pas Nema 17 sur les deux grosses pièces en plastique à l'aide de 8 vis M3 (8 mm de long).

- Insérez 8 écrous M3 dans les porte-écrous du chariot carré inférieur et placez-le en supportant les roulements linéaires LM8UU que vous avez insérés dans les longues tiges lisses déjà installées.
  
- Prenez les deux tiges lisses restantes (les plus courtes) et insérez deux roulements linéaires LM8UU sur chacune d'elles.

- Insérez les deux pièces d'extrémité à chaque extrémité de la paire de tiges lisses. Vous avez maintenant terminé le deuxième axe.

- Insérez le chariot carré supérieur sur les 4 roulements linéaires des tiges lisses les plus courtes.

- Insérez 4 vis M30 de 30 mm de long dans les 4 trous centraux du chariot carré supérieur, retournez le chariot avec précaution afin que la tête des vis repose sur la table et que les vis pointent vers le haut.

- Insérez un roulement F623ZZ avec la bride vers le bas, ensuite une rondelle M3 et enfin un autre roulement mais maintenant avec la bride vers le haut) dans chacune des quatre vis du chariot carré supérieur.

- Utilisez un post-it ou un morceau de papier de taille similaire pour le presser contre chacune des vis qui dépassent afin que le papier soit perforé et appuie contre le haut des roulements. Le but est que ce papier les maintienne en place pendant que nous renversons le tout pour éviter que les roulements ne tombent.

- Placez le chariot supérieur sur le chariot inférieur de manière à ce que les tiges lisses du haut forment un angle droit avec les tiges lisses du bas.

- Vissez légèrement chacune des quatre vis M3 et une fois que vous remarquez que chacune est fixée à l'écrou en bas, déchirez le papier post-it. Terminez ensuite de serrer les vis et ajoutez les 4 autres vis M3 de 30 mm qui n'ont pas de roulement mais ajoutent de la solidité à l'union des parties supérieure et inférieure du chariot.

- Placez une poulie GT2 sur chaque moteur pas à pas mais ne serrez pas encore le boulon sans tête.

- Placez une paire de roulements F623ZZ avec une rondelle M3 entre les deux fixée avec une vis M3 dans la partie d'extrémité Y qui supportera la partie servo.

- Insérez la courroie tout au long de son parcours (les traversées du chariot central sont un peu délicates). Et une fois que les poulies sont alignées avec la courroie, serrez les vis sans tête sur chacune d'elles.

- Utilisez deux vis M3 et deux écrous pour fixer la pièce de support du servo et ajoutez ensuite le microsevo à l'aide des deux vis qui l'accompagnent.

- Assurez-vous que les deux trous verticaux de la pièce support du servo ont un diamètre de 4 mm et que les tubes en fibre de carbone peuvent y être insérés (sinon, percez les trous avec un foret de 4 mm). Insérez les deux tubes par le haut mais seulement à mi-chemin. Et ensuite insérez par le haut le chariot vertical (celui qui ressemble à un visage souriant). Poussez-le doucement vers le bas jusqu'à ce que vous puissiez insérer la moitié restante des tubes en fibre de carbone afin qu'ils soient insérés dans les trous inférieurs de ce chariot.

- À l'aide de quelques vis et écrous M3, fixez la partie porte-stylo au chariot vertical.

- Poussez le support Arduino dans les tiges lisses saillantes de l'un des supports de moteur pas à pas. Utilisez quelques vis M3 pour fixer la carte Arduino au support en plastique.

BOM

- 4 tiges lisses de 8 mm (deux de 400 mm de long et deux de 320 mm de long)
- 8 LM8UU
- 2 poulies GT2 20 dents
- 10 roulements F623ZZ
- 1 ceinture GT2 ( 1,4 mètres de long )
- 2 tiges filetées M10 (400 mm de long chacune)
- 8 écrous M10
- 8 vis M3 de 30 mm avec écrous
- 8 vis M3 de 6 mm
- 4 vis M3 de 16 mm avec écrous
- 4 rondelles M3
- 2 tubes en fibre de carbone de 4 mm de diamètre extérieur et de 100 mm de long
- 2 vis M3 de 15 mm

Électronique:
- 2 steppers nema 17 (*)
- 1 micro servo SG90 (plus une rallonge de câble de 250 mm)
- 1 Arduino UNO
- 1 bouclier CNC
- 2 Mezzanine Pololu
- 1 alimentation 12V 2A
- 1 câble USB

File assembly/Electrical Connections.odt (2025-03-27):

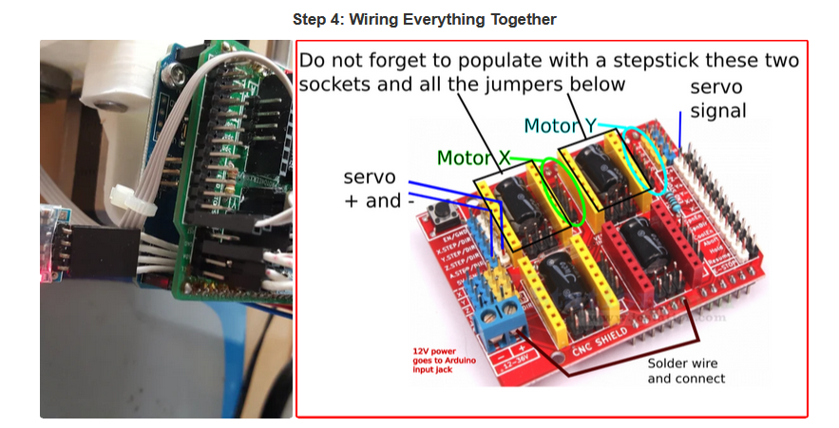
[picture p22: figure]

From file : https://www.instructables.com/4xiDraw/

Before inserting the CNCShield over the Arduino you want to do this trick (http://3dpburner.blogspot.com.es/p/bluetooth-connection.html), that will allow to power everything from the Arduino power jack. Failing to do this connection from Vin to + header on CNCShield most likely will make your servo not to work properly.

On top of Arduino you insert the CNCShield board and on top of it, two of the Pololu StepStick stepper driver boards. But before inserting these two boards for axis X and Y, make sure you put three jumpers in the headers (that will later be obstructed by the Pololu carrier boards).

A three-wire cable will be coming from the servo and two four-wire cables come from the stepper motors.

Servo cable has to go to (red) +5V, (black) GND and signal (white or brown) to Digital pin 11. Servo cable is too short, so an 250mm extension cable will be needed.

Each stepper motor goes to X and Y axis four pin headers on the CNCShield.

There is an optional improvement: make the plotter wireless by adding a Bluetooth module, but I would only do this once everything else is up and running.

From File : CNC-Shield-Guide-v1.0.pdf

Component Assembly

Below is a general outline process for connection of the various components:

1. Taking normal static electricity precautions, insert the CNC Shield into the Arduino Uno making sure the

correct pins of the CNC Shield are inserted into the correct UNO headers.

2. Decide on the micro stepper setting for your application and place the jumpers as required

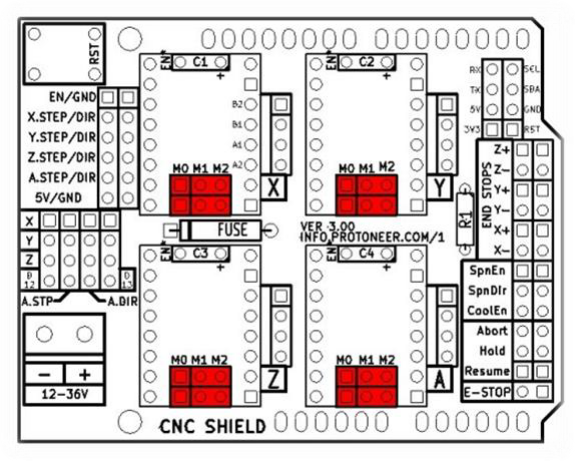
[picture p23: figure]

In the tables below High indicates that a Jumper is insert and Low indicates that no jumper is inserted.

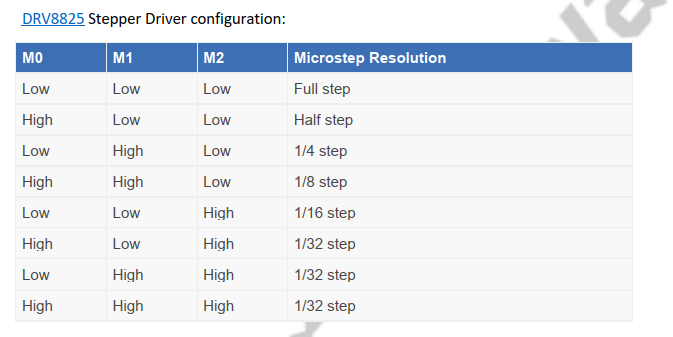
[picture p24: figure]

Push button connections

Cable colour | Button | Description
Black | E Stop | Arduino Reset
Green | Resume | Resume printing
Red | Hold | Hold printing
Blue | ABORT | Abort present printing
Orange | GND

From File : NEMA17-schneider.pdf

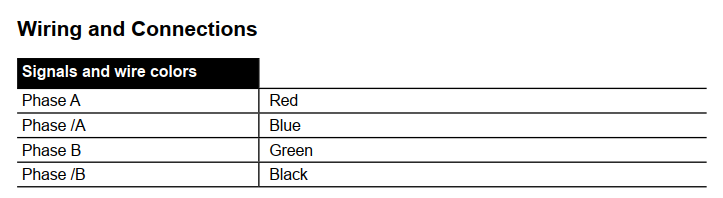
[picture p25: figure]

From File : 42SHD0001.jpeg

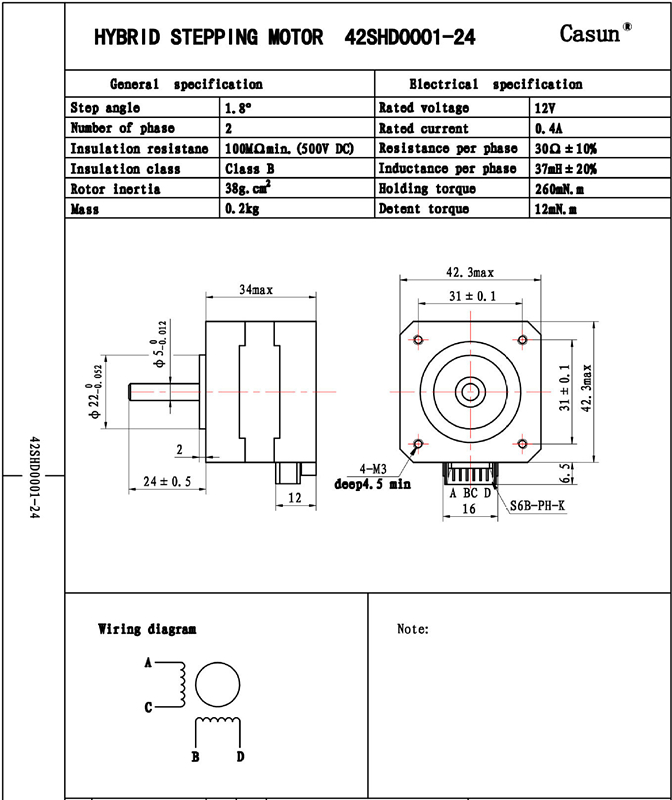
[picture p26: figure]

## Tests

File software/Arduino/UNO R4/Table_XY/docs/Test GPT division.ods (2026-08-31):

counter value | Time [msec] | Tick 1 count [usec] | Count freq [MHz] | Division | TPCS
15000 | 5,012 | 0,33413 | 2,993 | 16 | 4
3000 | 1,003 | 0,33433 | 2,991 | 16 | 4
8000 | 2,673 | 0,33413 | 2,993 | 16 | 4
15000 | 1,253 | 0,08353 | 11,971 | 4 | 3
3000 | 0,25 | 0,08333 | 12,000 | 4 | 3
8000 | 0,668 | 0,08350 | 11,976 | 4 | 3
15000 | 1,253 | 0,08353 | 11,971 | 4 | 2
3000 | 0,25 | 0,08333 | 12,000 | 4 | 2
8000 | 0,668 | 0,08350 | 11,976 | 4 | 2
15000 | 0,313 | 0,02087 | 47,923 | 1 | 1
3000 | 0,0624 | 0,02080 | 48,077 | 1 | 1
8000 | 0,1667 | 0,02084 | 47,990 | 1 | 1
15000 | 0,313 | 0,02087 | 47,923 | 1 | 0
3000 | 0,0624 | 0,02080 | 48,077 | 1 | 0
8000 | 0,1667 | 0,02084 | 47,990 | 1 | 0
90000 | 1,879 | 0,02088 | 47,898 | 1 | 0
18000 | 0,3758 | 0,02088 | 47,898 | 1 | 0
48000 | 1,002 | 0,02088 | 47,904 | 1 | 0

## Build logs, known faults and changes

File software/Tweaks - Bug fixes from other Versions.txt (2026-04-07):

- Tweak: Grbl now forces a buffer sync or stop motion whenever a g-code command needs to update and write a value to EEPROM or changes the work coordinate offset.

    - This addresses two old issues in all prior Grbl versions. 
	First, an EEPROM write requires interrupts to be disabled, including stepper and serial comm. Steps can be lost and data can be corrupted. 
	Second, the work position may not be correlated to the actual machine position, since machine position is derived from the actual current execution state, while work position is based on the g-code parser offset state.
	They are usually not in sync and the parser state is several motions behind. This forced sync ensures work and machine positions are always correct.
    - This behavior can be disabled through a config.h option, but it’s not recommended to do so.

- Tweak: TX buffer size has been increased from 64 to 90 bytes to improve status reporting and overall performance.

- Tweak: Grbl’s serial buffer increased by +1 internally, such that 128 bytes means 128, not 127 due to the ring buffer implementation. Long overdue.

- Refactor: Single character printPgmStrings() went converted to direct serial_write() commands to save significant flash space.

===================== Version 1.0
- Bug Fix: Applied v0.9 master fixes to CoreXY homing.

- Bug Fix: The print float function would cause Grbl to crash if a value was 1e6 or greater. Increased the buffer by 3 bytes to help prevent this in the future.

- Bug Fix: Build info and startup string EEPROM restoring was not writing the checksum value.

- Bug Fix: Corrected an issue with safety door restoring the proper spindle and coolant state. It worked before, but breaks with laser mode that can continually change spindle state per planner block.

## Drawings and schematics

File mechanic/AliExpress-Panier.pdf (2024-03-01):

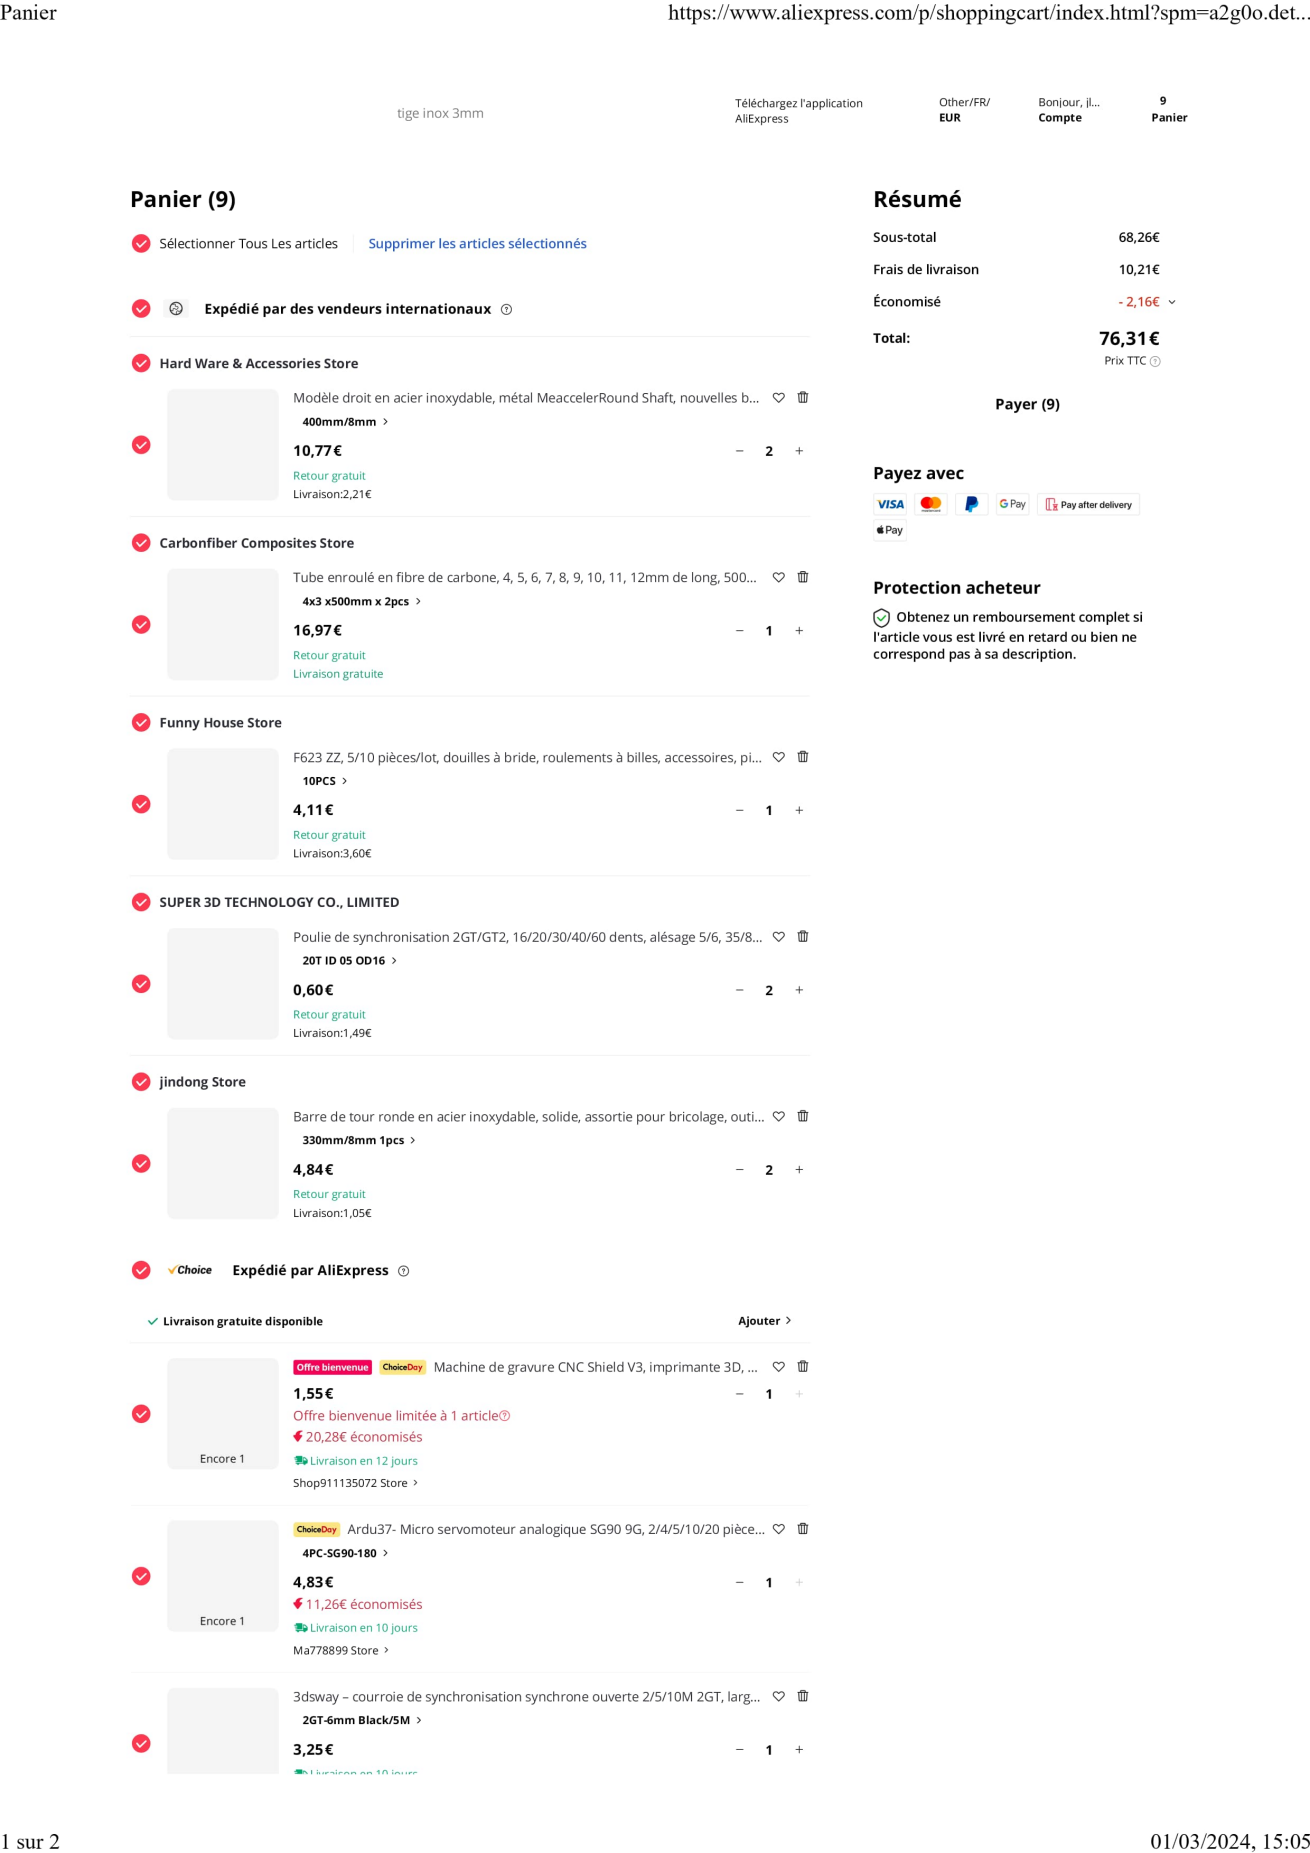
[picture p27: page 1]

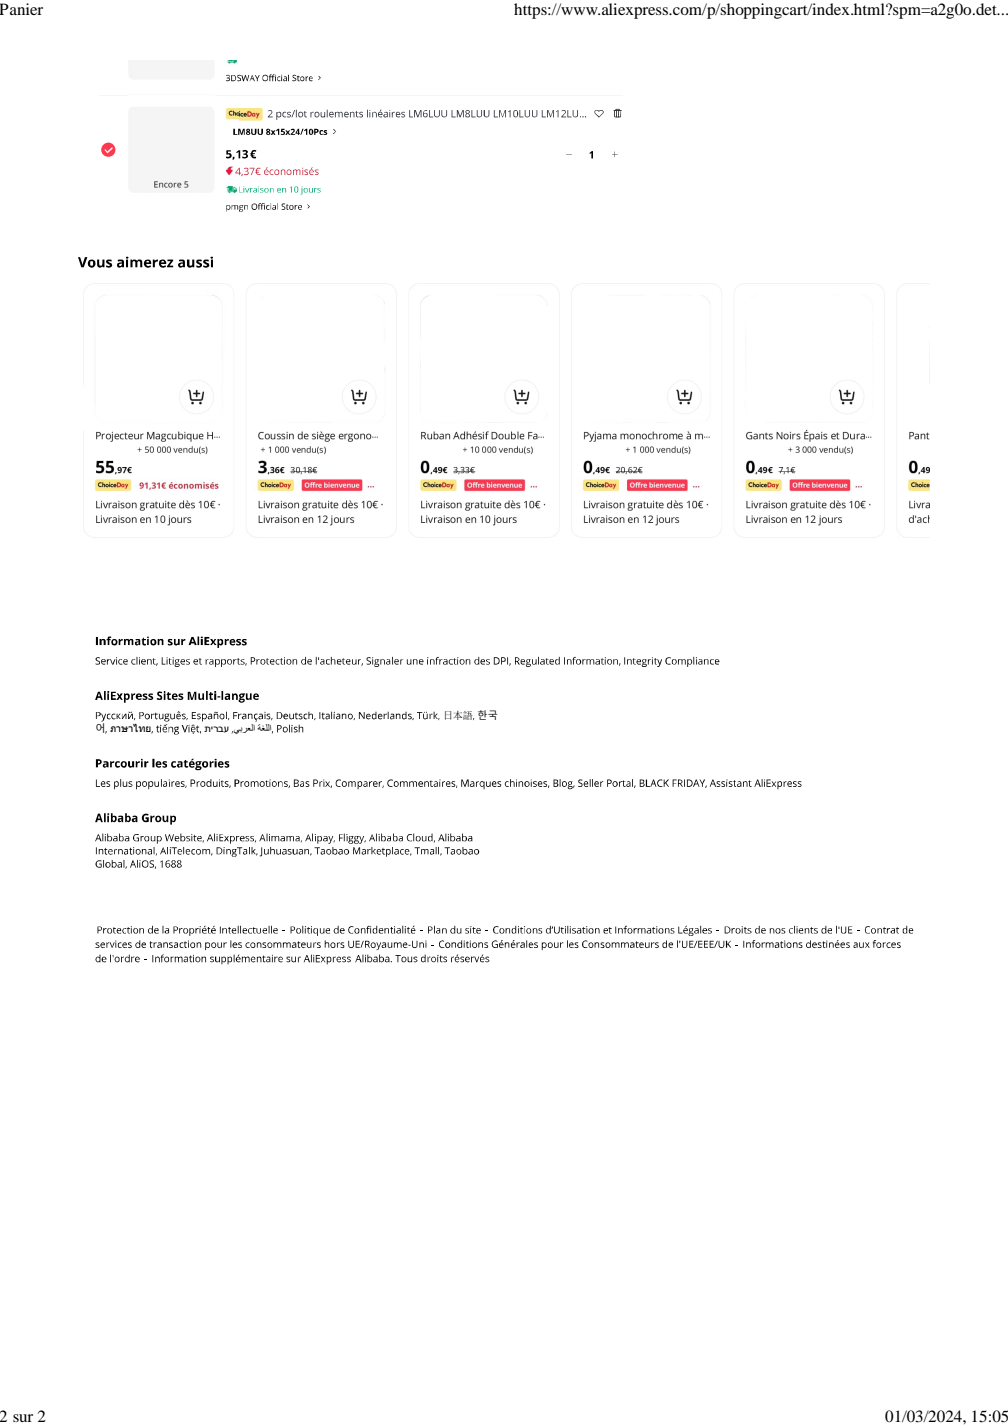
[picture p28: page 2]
日本語 한국; Panier; https://www.aliexpress.com/p/shoppingcart/index.html?spm=a2g0o.det...; 2 sur 2

ةغللا يبرعلا תירבע ภาษาไทย 어

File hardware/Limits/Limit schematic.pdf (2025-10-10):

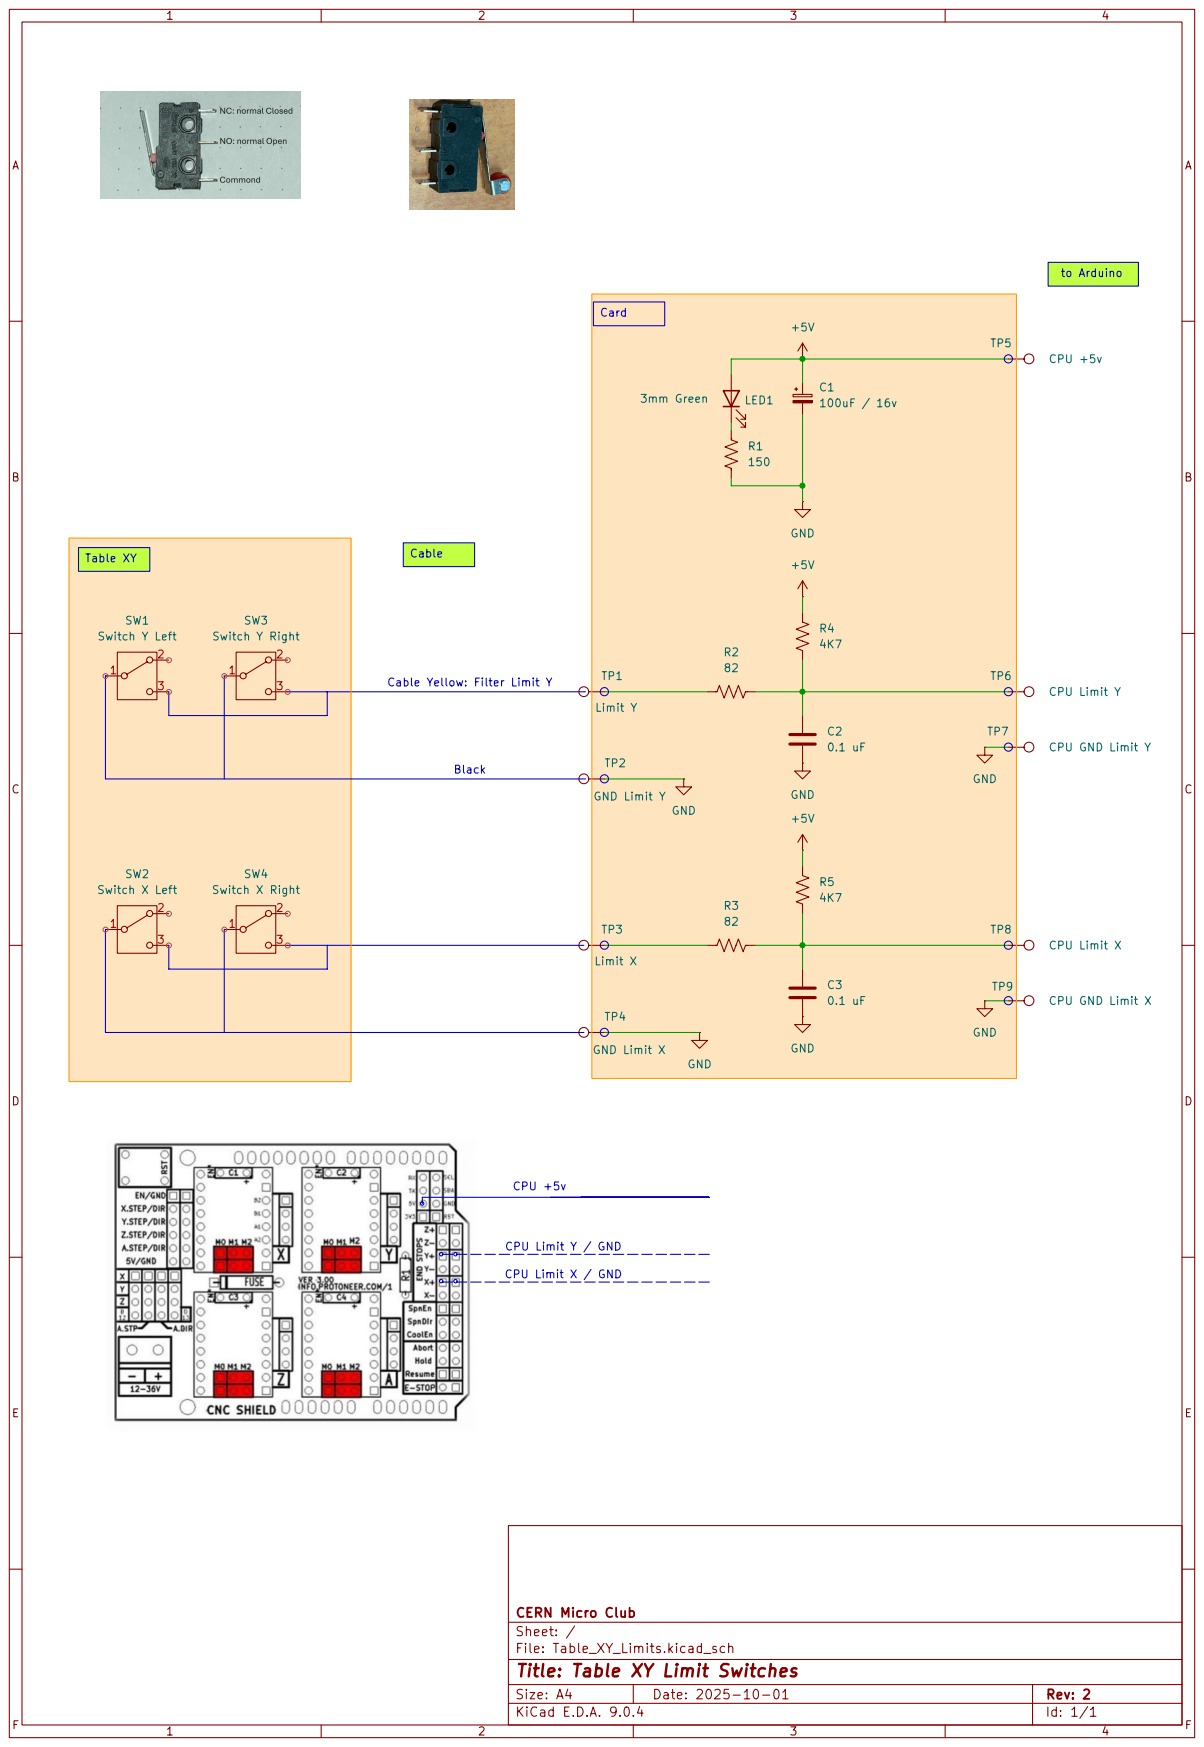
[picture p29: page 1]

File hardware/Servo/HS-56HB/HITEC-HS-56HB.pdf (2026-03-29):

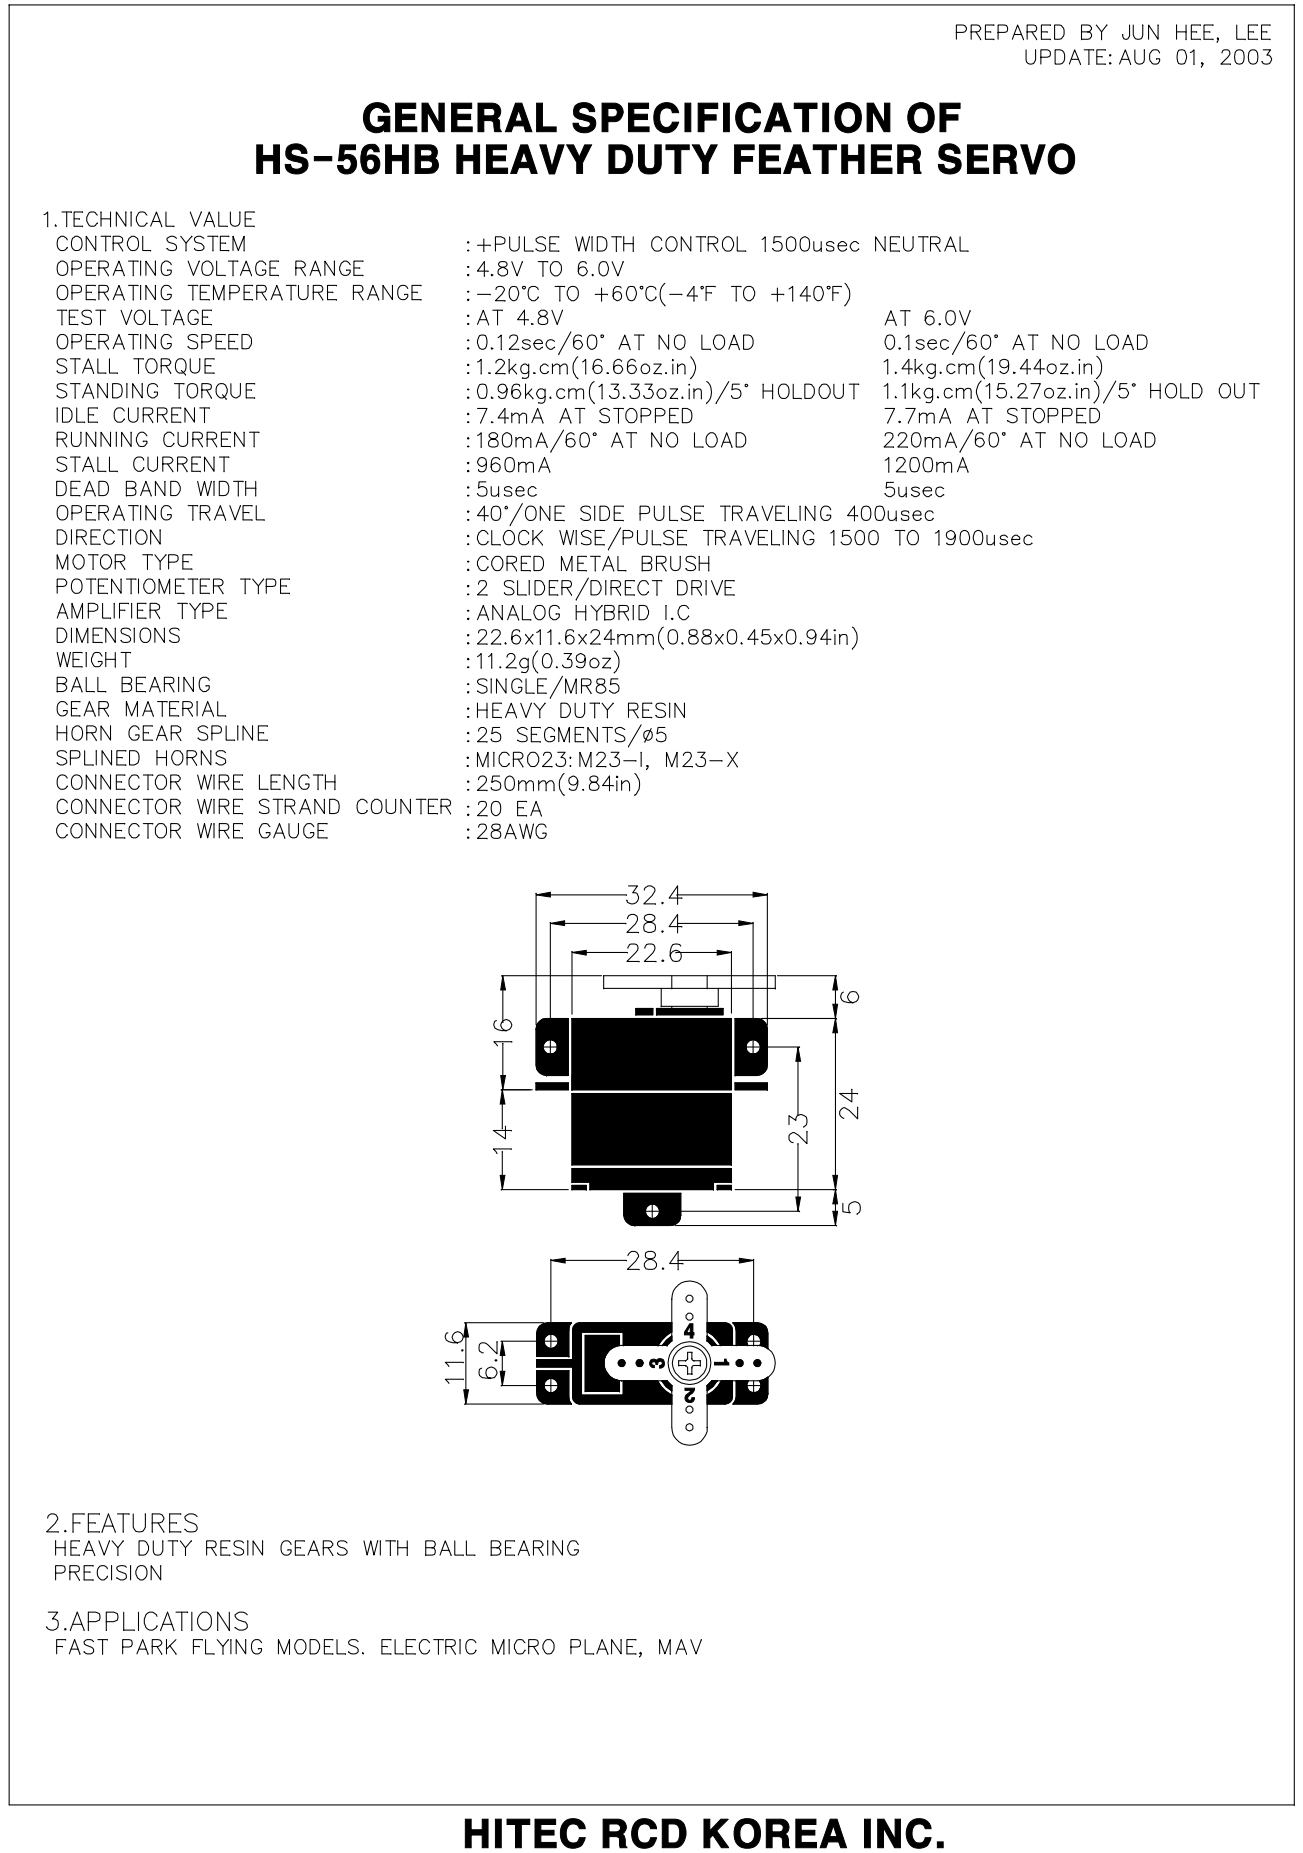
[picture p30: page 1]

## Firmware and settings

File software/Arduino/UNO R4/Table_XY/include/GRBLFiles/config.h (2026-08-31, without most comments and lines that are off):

#define config_h
#include "grbl.h" // For Arduino IDE compatibility.
#define CPU_MAP_RENESAS_R7FA4M1AB // Arduino Uno R4 CPU
#define DEFAULTS_GENERIC
#define BAUD_RATE 115200
#define CMD_STATUS_REPORT '?'
#define CMD_FEED_HOLD '!'
#define CMD_CYCLE_START '~'
#define CMD_RESET 0x18 // ctrl-x.
#define CMD_SAFETY_DOOR '@'
#define HOMING_INIT_LOCK // Comment to disable
#define HOMING_CYCLE_0 ((1<<X_AXIS)|(1<<Y_AXIS))
#define N_HOMING_LOCATE_CYCLE 1 // Integer (1-128)
#define N_STARTUP_LINE 2 // Integer (1-2)
#define N_DECIMAL_COORDVALUE_INCH 4 // Coordinate or position value in inches
#define N_DECIMAL_COORDVALUE_MM   3 // Coordinate or position value in mm
#define N_DECIMAL_RATEVALUE_INCH  1 // Rate or velocity value in in/min
#define N_DECIMAL_RATEVALUE_MM    0 // Rate or velocity value in mm/min
#define N_DECIMAL_SETTINGVALUE    3 // Decimals for floating point setting values
#define MESSAGE_PROBE_COORDINATES // Enabled by default. Comment to disable.
#define SAFETY_DOOR_SPINDLE_DELAY 4000
#define SAFETY_DOOR_COOLANT_DELAY 1000
#define COREXY // Default disabled. Uncomment to enable.
#define ACCELERATION_TICKS_PER_SECOND 100
#define ADAPTIVE_MULTI_AXIS_STEP_SMOOTHING  // Default enabled. Comment to disable.
#define TOOL_LENGTH_OFFSET_AXIS Z_AXIS // Default z-axis. Valid values are X_AXIS, Y_AXIS, or Z_AXIS.
#define MINIMUM_JUNCTION_SPEED 0.0 // (mm/min)
#define MINIMUM_FEED_RATE 1.0 // (mm/min)
#define N_ARC_CORRECTION 12 // Integer (1-255)
#define ARC_ANGULAR_TRAVEL_EPSILON 5E-7 // Float (radians)
#define DWELL_TIME_STEP 50 // Integer (1-255) (milliseconds)
#define STEP_PULSE_WIDTH_DEFAULT 10 // Step pulse width [usec] for initialisation
#if defined(USE_SPINDLE_DIR_AS_ENABLE_PIN) && !defined(VARIABLE_SPINDLE)
  #error "USE_SPINDLE_DIR_AS_ENABLE_PIN may only be used with VARIABLE_SPINDLE enabled"
#endif
#if defined(USE_SPINDLE_DIR_AS_ENABLE_PIN) && !defined(CPU_MAP_ATMEGA328P)
  #error "USE_SPINDLE_DIR_AS_ENABLE_PIN may only be used with a 328p processor"
#endif

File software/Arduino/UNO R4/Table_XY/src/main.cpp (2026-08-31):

/*
  main.c - An embedded CNC Controller with rs274/ngc (g-code) support
  Part of Grbl

  Copyright (c) 2026 	  Gomez Costa J.L.
  Copyright (c) 2011-2015 Sungeun K. Jeon
  Copyright (c) 2009-2011 Simen Svale Skogsrud

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
  You should have received a copy of the GNU General Public License
  along with Grbl.  If not, see <http://www.gnu.org/licenses/>.
*/

#define MAIN_FILE

#include <grbl.h>

#include <Arduino.h>
#include <stdlib.h>
#include <stdint.h>
#include <stdbool.h>
#include <string.h>
#include <math.h>

// Declare system global variable structure
system_t sys;


//-----------------------------------------------------------------------------------------
//-----------------------------------------------------------------------------------------
void setup(void){

  char revision[90];
  fsp_err_t return_value;

  strcpy(revision, VERSION_NUMBER); strcat(revision, " ");
  strcat(revision, VERSION_BUILD_DAY); strcat(revision, "/");
  strcat(revision, VERSION_BUILD_MONTH); strcat(revision, "/");
  strcat(revision, VERSION_BUILD_YEAR); strcat(revision, " ");

  displayMatrixLED(revision, 2);

  // Initialize system upon power-up.

  #ifdef DEBUG_TEST_1_TEST_2
  // TEST 1 pin collides with COOLANT MIST pin
  // If used, COOLANT nust be disabled
  debugPinOutputTest_1_init();

  // TEST 2 pin collides with PROBE pin
  // If used, PROBE nust be disabled
  debugPinOutputTest_2_init();
  #endif


  debugPinOutputTest_3_init();

  serial_init();    // Setup serial baud rate and interrupts

  // Initialisation of Flash Data
  return_value = Flash_init();

  if (return_value != FSP_SUCCESS){
    __enable_irq(); // Enable interrupts for accessing Serial data
    displayFlashError("Initialisation", return_value);
    //Program will stay here
  };

  __enable_irq(); // Enable interrupts

  settings_init(); // Load Grbl settings from EEPROM
  stepper_init();  // Configure stepper pins and interrupt timers
  system_init();   // Configure pinout pins

  memset(&sys, 0, sizeof(sys));  // Clear all system variables
  sys.abort = true;   // Set abort to complete initialization

    // Check for power-up and set system alarm if homing is enabled to force homing cycle
  // by setting Grbl's alarm state. Alarm locks out all g-code commands, including the
  // startup scripts, but allows access to settings and internal commands. Only a homing
  // cycle '$H' or kill alarm locks '$X' will disable the alarm.
  // NOTE: The startup script will run after successful completion of the homing cycle, but
  // not after disabling the alarm locks. Prevents motion startup blocks from crashing into
  // things uncontrollably. Very bad.
  #ifdef HOMING_INIT_LOCK
    if (bit_istrue(settings.flags,BITFLAG_HOMING_ENABLE)) { sys.state = STATE_ALARM; }
  #endif

  // Force Grbl into an ALARM state upon a power-cycle or hard reset.
  #ifdef FORCE_INITIALIZATION_ALARM
    sys.state = STATE_ALARM;
  #endif

}

//-----------------------------------------------------------------------------------------
//-----------------------------------------------------------------------------------------
void loop() {

  // Grbl initialization loop upon power-up or a system abort. For the latter, all processes
  // will return to this loop to be cleanly re-initialized.
  for(;;) {

    // TODO: Separate configure task that require interrupts to be disabled, especially upon
    // a system abort and ensuring any active interrupts are cleanly reset.

    // Reset Grbl primary systems.
    serial_reset_read_buffer(); // Clear serial read buffer
    gc_init(); // Set g-code parser to default state
    spindle_init();
    coolant_init();
    probe_init();
    limits_init();
    plan_reset(); // Clear block buffer and planner variables
    st_reset();   // Clear stepper subsystem variables.

    AGT1_init();    // This must be executed after Initialising Limit and Control bits

    // Sync cleared gcode and planner positions to current system position.
    plan_sync_position();
    gc_sync_position();

    // Reset system variables.
    sys.abort = false;
    sys.rt_exec_state = 0;
    sys.rt_exec_alarm = 0;
    sys.suspend = false;

    // Start Grbl main loop. Processes program inputs and executes them.
    protocol_main_loop();

  }
  // Never reached
}

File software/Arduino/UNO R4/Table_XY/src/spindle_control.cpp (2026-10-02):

/*
  spindle_control.c - spindle control methods
  Part of Grbl

  Copyright (c) 2026 	  Gomez Costa J.L.
  Copyright (c) 2012-2015 Sungeun K. Jeon
  Copyright (c) 2009-2011 Simen Svale Skogsrud

  Grbl is free software: you can redistribute it and/or modify
  it under the terms of the GNU General Public License as published by
  the Free Software Foundation, either version 3 of the License, or
  (at your option) any later version.
  Grbl is distributed in the hope that it will be useful,
  but WITHOUT ANY WARRANTY; without even the implied warranty of
  MERCHANTABILITY or FITNESS FOR A PARTICULAR PURPOSE.  See the
  GNU General Public License for more details.
  You should have received a copy of the GNU General Public License
  along with Grbl.  If not, see <http://www.gnu.org/licenses/>.
*/


/* RC-Servo PWM modification: switch between 0.6ms and 2.5ms pulse-width at 61Hz
   Prescaler 1024 = 15625Hz / 256Steps =  61Hz	64µs/step -> Values 15 / 32 for 1ms / 2ms
   Reload value = 0x07
   Replace this file in C:\Program Files (x86)\Arduino\libraries\GRBL
*/


#include "grbl.h"


void spindle_init()
{
  // Configure variable spindle

  GPT16_PERIPHERAL_ENABLE;    // Enable GPT Peripheral before accessing

  //Servo pin
  PFS_WRITE_ENABLE;

  // Define Bit as GPT
  R_PFS->PORT[SERVO_CPU_PORT].PIN[SERVO_CPU_BIT].PmnPFS = 0UL;          // Init all bits to 0, standard setting
  R_PFS->PORT[SERVO_CPU_PORT].PIN[SERVO_CPU_BIT].PmnPFS_b.PDR = 1;      //Output
  R_PFS->PORT[SERVO_CPU_PORT].PIN[SERVO_CPU_BIT].PmnPFS_b.PMR = 1;      //Peripheral
  R_PFS->PORT[SERVO_CPU_PORT].PIN[SERVO_CPU_BIT].PmnPFS_b.PSEL = 0x03;  //GTIOC6A

  PFS_WRITE_DISABLE;

  //---------------------------------------------------------------------------------------------------------------
  //Servo PWM Timer
  GPT_REG_WRITE_ENABLE(R_GPT6);

  R_GPT6->GTCR = 0;             // Clear Register
  R_GPT6->GTCR_b.CST = 0;       // GPT Stop
  R_GPT6->GTCR_b.MD = 0;        // Saw-wave PWM mode (single buffer or double buffer possible)
  R_GPT6->GTCR_b.TPCS = SERVO_GPT6_TPCS;      // Clock %

  R_GPT6->GTUDDTYC = 0;             // Clear Register
  R_GPT6->GTUDDTYC_b.UD = 1;        // GTCNT count up
  R_GPT6->GTUDDTYC_b.OADTY = 0x00;  // GTIOCA pin duty depends on compare match

  R_GPT6->GTIOR = 0;                // Clear Register
  R_GPT6->GTIOR_b.GTIOA = 0x09;     // Initial output is low, High output at cycle end, Low output at GTCCRA/GTCCRB compare match
  R_GPT6->GTIOR_b.OADFLT = 0;       // GTIOCA Pin Output Value Setting at the Count Stop: The GTIOCA pin outputs low when counting stops
  R_GPT6->GTIOR_b.OAE = 1;          // GTIOCA Pin Output Enable
  R_GPT6->GTIOR_b.OADF = 0;         // GTIOCA Pin Disable value setting

  R_GPT6->GTBER_b.BD0 = 0;        // Timer buffer enable Register: Buffer is enabled GTCCR
  R_GPT6->GTBER_b.BD1 = 0;        // Buffer is enabled GTPR
  R_GPT6->GTBER_b.CCRA = 1;       // GTCCRA: single buffer
  R_GPT6->GTBER_b.PR = 1;         // GTPR: single buffer

  R_GPT6->GTCNT = 0;                // Ramp Counter
  R_GPT6->GTPR_b.GTPR = SERVO_MAX_COUNTER;  // Max counter for setting the Servo Period
  R_GPT6->GTPBR_b.GTPBR = SERVO_MAX_COUNTER;

  SERVO_REGISTER_VALUE = SERVO_COUNT_1MSEC;   // Compare Register for Servo

  R_GPT6->GTSSR_b.CSTRT = 1;    // Start source: Software start
  R_GPT6->GTSTR_b.CSTRT6 = 1;   // Start
  R_GPT6->GTCR_b.CST = 1;       // GPT Start

  GPT_REG_WRITE_DISABLE(R_GPT6);

  spindle_run(SPINDLE_DISABLE,0);  // Define initial position as Pencil Up
}

//-----------------------------------------------------------------------------
// Names are kept kept for compatibility with the main GRBL files, but it is not used
//
//  Parameters:
//    direction:
//      action to be taken
//        Pencil UP:    SPINDLE_DISABLE (M5)
//        Pencil Down:  SPINDLE_ENABLE_CW (M3) or SPINDLE_ENABLE_CCW (M4)
//
//    rpm: comes for gc_state.spindle_speed
//      Parameter S in M3/ M4 is not used when Pencil is installed
//

void spindle_run(uint8_t direction, float rpm)
{
  if (sys.state == STATE_CHECK_MODE) { return; }

  // Empty planner buffer to ensure spindle is set when programmed.
  protocol_auto_cycle_start();  //temp fix for M3 lockup
  protocol_buffer_synchronize();

  if (direction == SPINDLE_DISABLE) {

    spindle_stop();

  } else {

    GPT_REG_WRITE_ENABLE(R_GPT6);

    if(RC_SERVO_INVERT){
      SERVO_REGISTER_VALUE = PWM_COUNTER_MIN;
    }else{
      SERVO_REGISTER_VALUE = PWM_COUNTER_MAX;
    }

    GPT_REG_WRITE_DISABLE(R_GPT6);

  }
}



void spindle_stop()
{

GPT_REG_WRITE_ENABLE(R_GPT6);

if(RC_SERVO_INVERT){
  SERVO_REGISTER_VALUE = PWM_COUNTER_MAX;
}else{
  SERVO_REGISTER_VALUE = PWM_COUNTER_MIN;
}

GPT_REG_WRITE_DISABLE(R_GPT6);

}

// Not used as it is Pencil up/down
void spindle_set_state(uint8_t state, float rpm){

}
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

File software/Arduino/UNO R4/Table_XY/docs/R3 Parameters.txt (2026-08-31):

Grbl 0.9i ['$' for help]

$0 = 10    (step pulse, usec)
$1 = 25    (step idle delay, msec)
$2 = 0    (step port invert mask:00000000)
$3 = 0    (dir port invert mask:00000000)
$4 = 0    (step enable invert, bool)
$5 = 0    (limit pins invert, bool)
$6 = 0    (probe pin invert, bool)
$10 = 3    (status report mask:00000011)
$11 = 0.010    (junction deviation, mm)
$12 = 0.002    (arc tolerance, mm)
$13 = 0    (report inches, bool)
$20 = 0    (soft limits, bool)
$21 = 0    (hard limits, bool)
$22 = 0    (homing cycle, bool)
$23 = 0    (homing dir invert mask:00000000)
$24 = 25.000    (homing feed, mm/min)
$25 = 500.000    (homing seek, mm/min)
$26 = 250    (homing debounce, msec)
$27 = 1.000    (homing pull-off, mm)
$100 = 250.000    (x, step/mm)
$101 = 250.000    (y, step/mm)
$102 = 250.000    (z, step/mm)
$110 = 2000.000    (x max rate, mm/min)
$111 = 2000.031    (y max rate, mm/min)
$112 = 2000.000    (z max rate, mm/min)
$120 = 10.000    (x accel, mm/sec^2)
$121 = 10.000    (y accel, mm/sec^2)
$122 = 10.000    (z accel, mm/sec^2)
$130 = 200.000    (x max travel, mm)
$131 = 200.000    (y max travel, mm)
$132 = 200.000    (z max travel, mm)

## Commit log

2023-11-14 Added Directory tree
    [DrawingMachine_-_Arduino_grip.stl, DrawingMachine_-_Pen_Carriage_1.stl, DrawingMachine_-_Pen_holder_1.stl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]
2023-11-14 Updated Pieces.ods
    [Piéces.ods]
2023-11-14 Added components
    [Piéces.ods]
2023-11-16 Deleted all image files, transferred to wiki_images
    [DrawingMachine_-_Arduino_grip.stl, DrawingMachine_-_Pen_Carriage_1.stl, DrawingMachine_-_Pen_holder_1.stl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]
2023-11-16 pieces.ods changed to Bill-of-Materials.ods
    [Bill-of-Materials.ods]
2023-11-16 Eliminated spaces in Directory names
    [DrawingMachine_-_Arduino_grip.stl, DrawingMachine_-_Pen_Carriage_1.stl, DrawingMachine_-_Pen_holder_1.stl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]
2023-11-16 Change in name Print-3D -> print-3D
2024-01-08 Added Prusa 3D files, Changed Directory name
    Updated Directory name:
    - GitHub\Table-XY\mechanic\print-3D -> GitHub\Table-XY\mechanic\Files
    [DrawingMachine_-_Arduino_grip.stl, DrawingMachine_-_Pen_Carriage_1.stl, DrawingMachine_-_Pen_holder_1.stl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]
2024-01-18 Update PRUSA 3D printer
    Updated:
    3D Printer: i3 MK3S & MK3S+
    Impression 0.15 mm
    [TableXY-Part1.3mf, TableXY-Part2.3mf, TableXY-Part3.3mf]
2024-01-18 Updated documents
    [BillOfMaterials.ods]
2024-01-19 Modify filament to 1.75mm
    [TableXY-Part1.3mf, TableXY-Part2.3mf, TableXY-Part3.3mf]
2024-02-02 Bill of Materials: Added AliExpress cost
    [Bill-of-Materials.ods, BillOfMaterials.ods]
2024-03-01 Added Components: AliExpress-Panier.pdf
    [Bill-of-Materials.ods]
2024-05-28 Create Table-XY-link.txt
    Added Link to Table-XY mounting description .
2024-05-28 Added assembly steps in French and English
2024-06-06 Updated Assembly\Table-XY-links.txt with link to CAD-3D
2024-10-12 Added photos of connectors
2024-10-18 Added electrical connections, document file reorder
    [Motor-Comparison.ods]
2024-10-23 Added Servo SG92R docs
2024-10-29 Updated Assembly connections
    Stepper motor to CNC pin-out must be checked
    [Connections.ods]
2024-11-01 Updated Connections
    ToDo: check 42SHD0001 pin-out
    [Connections.ods]
2024-11-05 Documentation for stepping motor connections
    [Connections.ods]
2024-11-07 Updated Stepper motor connections. Added Photos
    [Connections.ods, Stepper Motor-Servo Connections.ods]
2025-02-26 Added documents for CNC shield and pin-out
    [Pinout UNO R3_R4.ods, Stepper Motor-Servo Connections.ods]
2025-02-26 Update Pinout UNO R3_R4.ods
    [Pinout UNO R3_R4.ods]
2025-03-17 Updated hardware docs
    [Pinout UNO R3_R4.ods]
2025-03-25 Corrected Pin-Out file for CNC control
    [Pinout UNO R3_R4.ods]
2025-03-25 Added Button features
    [Pinout UNO R3_R4.ods]
2025-03-27 Added Push button connections
2025-03-27 Added Button connections
2025-03-28 File {Electrical Connections.odt} replaced by {General Information - Connections.odt}
    General Information - Connections.odt
    Added Servo and Software information
    [Stepper Motor-Servo Connections.ods]
2025-03-28 Added Limit switch
2025-03-28 Updated some Servo information
2025-04-25 Create Configuration.txt
    Somme interesting configuration for adapting software to hardware
    [Configuration.txt]
2025-09-18 Add gcode sample
2025-10-10 Added Limit circuit
2025-10-11 Added Limit switches and Filtering
2025-10-13 Updated Document, re-arranged directories
    [Bill-of-Materials.ods]
2025-10-18 Added Mechanics for FilterCard
    GCode directory transferred to Software
    [Support_LimitSwitchFilterCard.stl]
2026-02-25 Added mechanics for support Limit Switch card
    [Support_LimitSwitch_FilterCard.3mf, Support_LimitSwitch_FilterCard.stl]
2026-02-25 Updated 3DPrinter Prusa Type and filament
    [Support_LimitSwitch_FilterCard.3mf]
2026-03-22 Added GRBL Arduino programs
    [config.h, cpu_map.h, defaults.h]
2026-03-27 Version 0.550
    [config.h, cpu_map.h, defaults.h]
2026-03-29 Zipped grbl-servo-master
    [config.h, cpu_map.h, defaults.h]
2026-04-03 Adjusting GRBL version 1.1h
    [alarm_codes_en_US.csv, build_option_codes_en_US.csv, config.h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]
2026-04-04 Prepared Grbl 1..1h for a new approach for spindle pencil control
2026-04-07 Changed Directory name
    TableXY_grbl_v1.1h\grbl -> TableXY_grbl_v1.1h\TableXY_grbl_v1.1h
    [config.h, cpu_map.h, defaults.h]
2026-04-07 Canceled modification of grbl_v1.1h
    The differences between grbl 0.9i (Pencil control via spindle control) and grbl 1.1h are too important (almost complete refurbishing) for porting the Pencil control to the 1.1h
    [alarm_codes_en_US.csv, build_option_codes_en_US.csv, config.h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]
2026-04-07 Added Comments
    - Python script for serial communication to directory: software
    - Tweaks - Bug fixes from other Versions.txt some interesting modifications to add
    -Links GRBL v0.9.txt: links to version 0.9
    -
    [Links GRBL v0.9.txt, wireshark.csv]
2026-04-07 Version 0.7
    [Links GRBL v0.9.txt]
2026-04-13 Added python scripts for Gcode to GRBL controller
2026-05-07 Added PenHolder with larger place for pencil
    [DrawingMachine_-_Pen_holder_1.stl, PenHolder_base.stl, PenHolder_enlarged_3mm.stl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]
2026-05-07 Updates Prusa 3DPrinter type
    [PenHolder_enlarged_both.3mf]
2026-05-08 Eliminated Pinout docs
    [Pinout UNO R3_R4.ods]
2026-05-12 Enlarged Pen holder separated in two files
    [PenHolder_enlarged_long.3mf, PenHolder_enlarged_small.3mf]
2026-05-24 Added PenHolder inverse position
    [PenHolder_inverse.3mf]
2026-05-31 Added docs about Arduino UNO R3 I/O and peripherals
    [Table XY CPU UNO R3 peripherals.ods, Table XY pinout UNO R3.ods]
